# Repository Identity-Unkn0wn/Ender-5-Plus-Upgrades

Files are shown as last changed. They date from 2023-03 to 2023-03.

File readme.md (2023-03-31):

# Ender 5 Plus(E5+) Upgrades

This is just a collection of thing that I have done to my printer and wanted to consolidate the resources for anyone who may want to do the same. 

**WARNING:** This is still a work in progress.

## Table of Contents
- [Installation of Sprite Extruder](#installation-of-sprite-extruder)
- [Installation of BTT SKR 3EZ](#installation-of-btt-skr-3ez)
- [Klipper \& .CFGs](#klipper--cfgs)
- [EXTRAS](#extras)

# Installation of Sprite Extruder
* [Printing Sprite Extruder Parts](Installing%20Sprite%20Extruder/Printing%20Sprite%20Extruder%20Parts.md)
* [Installing Sprite Extruder](Installing%20Sprite%20Extruder/Installing%20Sprite%20Extruder.md)
* [Wiring Extruder](Installing%20Sprite%20Extruder/Wiring%20Extruder.md)

# Installation of BTT SKR 3EZ
* [Printing Motherboard (MB) Adapter](Installing%20BTT%20SKR%203EZ/Printing%20MB%20Adapter%20Plate.md)
* [Installation & Wiring](Installing%20BTT%20SKR%203EZ/Installing%20BTT%20SKR%203EZ.md)

# Klipper & .CFGs
* [Klipper Install](Klipper%20&%20.cfgs/Klipper-Mainsail%20install.md)
* [Flashing Printer MCU](Klipper%20&%20.cfgs/Flashing%20Printer%20MCU.md)
* [Mainsail](Klipper%20&%20.cfgs/Mainsail.md)

# EXTRAS
* [BL Touch (& sim)](Extra/Extra.md)

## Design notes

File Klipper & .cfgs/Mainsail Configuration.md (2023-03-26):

# Configuring Mainsail
This part is strictly how I did mine and you are more than welcome to modify and set up to your liking.

# Printer.cfg
* Select `MACHINE` in menu on the left side
* Find your printer.cfg file and select it
* Below will be what mine looks like, but yours will vary depending on how you set your printer up.
> 
```
# This file contains pin mappings for the Creality Ender 5 Plus.
# Ender 5 Plus stock uses a Creality v2.2 board, similar to CR-20 Pro.
# To use this config, the firmware should be compiled for the AVR
# atmega2560.

# See docs/Config_Reference.md for a description of parameters.

#[include timelapse.cfg] ## uncomment this if you choose to install timelapse feature
#[include macros.cfg] # I use a separate folder for my macros
[include mainsail.cfg]
[virtual_sdcard]
path: /home/ryan/Ender5Plus_data/gcodes ###Change this to your path
on_error_gcode: CANCEL_PRINT

[exclude_object]

######################################################################
# BED LEVELING
######################################################################

[bltouch]
sensor_pin: ^PC13
control_pin: PE5
x_offset:-31
y_offset:-41
#z_offset: 3.380
pin_up_reports_not_triggered: True
pin_up_touch_mode_reports_triggered: False
stow_on_each_sample: False
probe_with_touch_mode: True
speed:10
samples:2

[safe_z_home]
home_xy_position: 175, 175 # Change coordinates to the center of your print bed
speed: 100
z_hop: 10 # Move up 10mm
z_hop_speed: 20

[bed_mesh]
speed: 200
horizontal_move_z: 5
mesh_min: -4, -6
mesh_max: 320, 301
probe_count: 5, 5
mesh_pps: 2,2
fade_start: 1.0
fade_end: 10.0
fade_target: 0.0

[screws_tilt_adjust]
screw1: 58, 74
screw1_name: Front Left screw
screw2: 352, 338
screw2_name: Back Right
screw3: 352,74
screw3_name: Front Right
screw4: 58,338
screw4_name: Back Left
horizontal_move_z: 6
speed: 200
screw_thread: CW-M4

[z_tilt]  ### Will only need this if you connected both z axis motors to their own driver
z_positions: 22, 204
           351, 204
# A list of X,Y coordinates (one per line; subsequent lines
# indented) describing the location of each bed "pivot point". The
# "pivot point" is the point where the bed attaches to the given Z
# stepper. It is described using nozzle coordinates (the XY position
# of the nozzle if it could move directly above the point). The
# first entry corresponds to stepper_z, the second to stepper_z1,
# the third to stepper_z2, etc. This parameter must be provided.
points: 22, 204
      351, 204
          
# A list of X,Y coordinates (one per line; subsequent lines | back |
# indented) that should be probed during a Z_TILT_ADJUST command. | |
# Specify coordinates of the nozzle and be sure the probe is above L z1 z R
# the bed at the given nozzle coordinates. This parameter must be | |
# provided. | front |
speed: 200
horizontal_move_z: 7
retries: 20
# Number of times to retry if the probed points aren't within
# tolerance.
retry_tolerance:0.0025
# If retries are enabled then retry if largest and smallest probed
# points differ more than retry_tolerance. Note the smallest unit of
# change here would be a single step. However if you are probing
# more points than steppers then you will likely have a fixed
# minimum value for the range of probed points which you can learn
# by observing command output.

# This file contains common pin mappings for the BigTreeTech SKR 3.
# To use this config, the firmware should be compiled for the
# STM32H743 with a "128KiB bootloader".

# See docs/Config_Reference.md for a description of parameters.

######################################################################
# X Stepper
######################################################################

[stepper_x]
step_pin: PD4
dir_pin: !PD3
enable_pin: !PD6
microsteps: 16
rotation_distance: 40
endstop_pin: ^PC1
position_endstop: 352
position_max: 352
#position_min:-20  #used for getting my min
homing_speed: 150

[tmc2209 stepper_x]
uart_pin: PD5
run_current: 0.580
diag_pin:
interpolate: False #Comment out if you use stealth shop
#stealthchop_threshold: 999999 #will make your printer quieter, but at a cost to accuracy; this applies to all below

######################################################################
# Y Stepper
######################################################################

[stepper_y]
step_pin: PA15
dir_pin: !PA8
enable_pin: !PD1
microsteps: 16
rotation_distance: 40
endstop_pin: ^PC3
position_endstop: 342
position_max: 342
#position_min:-10
homing_speed: 150

[tmc2209 stepper_y]
uart_pin: PD0
run_current: 0.580
diag_pin:
interpolate: False
#stealthchop_threshold: 999999

######################################################################
# Z & Z1 Stepper
######################################################################

[stepper_z]
step_pin: PE2
dir_pin: !PE3
enable_pin: !PE0
microsteps: 16
rotation_distance: 4
endstop_pin: probe:z_virtual_endstop
#position_endstop: 0.5
position_max: 400
position_min: -6
homing_speed: 10.0

[tmc2209 stepper_z]
uart_pin: PE1
run_current: 0.580
diag_pin:
interpolate: False
#stealthchop_threshold: 999999

[stepper_z1]
step_pin: PD11
dir_pin: !PD10
enable_pin: !PD13
microsteps: 16
rotation_distance: 4
#endstop_pin: PC13
#position_endstop: 0.5
#position_max: 200

[tmc2209 stepper_z1]
uart_pin: PD12
run_current: 0.580
diag_pin:
interpolate: False
#stealthchop_threshold: 999999

######################################################################
# Extruder
######################################################################

[extruder]
step_pin: PD15
dir_pin: PD14
enable_pin: !PC7
microsteps: 16
gear_ratio: 42:12
rotation_distance: 26.4462726999097
nozzle_diameter: 0.400
filament_diameter: 1.750
heater_pin: PB3
sensor_type: EPCOS 100K B57560G104F
sensor_pin: PA2
#control: pid
#pid_Kp: 22.2
#pid_Ki: 1.08
#pid_Kd: 114
min_temp: 0
max_temp: 300
max_extrude_only_distance: 450
min_extrude_temp: 180
#pressure_advance: .1127

[tmc2209 extruder]
uart_pin: PC6
run_current: 0.650
diag_pin:
#stealthchop_threshold: 999999

######################################################################
# Heated Bed
######################################################################

[heater_bed]
heater_pin: PD7
sensor_type: EPCOS 100K B57560G104F
sensor_pin: PA1
#control: watermark
min_temp: 0
max_temp: 130

[fan]
pin: PB7

[heater_fan hotend_fan]
pin: PB6
heater: extruder
heater_temp:50.0

[heater_fan mcu_fan]
pin: PB5
heater_temp: 45.0

[mcu]
serial: /dev/serial/by-id/usb-Klipper_stm32h743xx_400029000B51303138393138-if00

[printer]
kinematics: cartesian
max_velocity: 300
max_accel: 3000
max_z_velocity: 5
max_z_accel: 100

########################################
# EXP1 / EXP2 (display) pins
########################################

[board_pins]
aliases:
    # EXP1 header
    EXP1_1=PC5, EXP1_3=PB1, EXP1_5=PE9,  EXP1_7=PE11, EXP1_9=<GND>,
    EXP1_2=PB0, EXP1_4=PE8, EXP1_6=PE10, EXP1_8=PE12, EXP1_10=<5V>,
    # EXP2 header
    EXP2_1=PA6, EXP2_3=PE7, EXP2_5=PB2, EXP2_7=PC4,   EXP2_9=<GND>,
    EXP2_2=PA5, EXP2_4=PA4, EXP2_6=PA7, EXP2_8=<RST>, EXP2_10=<NC>

[temperature_sensor raspberry_pi]
sensor_type: temperature_host
min_temp: 10
max_temp: 100

[temperature_sensor mcu_temp]
sensor_type: temperature_mcu
min_temp: 0
max_temp: 100

[filament_switch_sensor filament_sensor]
pause_on_runout: True
#runout_gcode: PAUSE
#insert_gcode: RESUME
switch_pin: PC2
```

## Cusomization

From here everything else would be your prefrence. I'll soon add a guide on how I tune my printer. I'll add links for anything I think would be useful in the [Extra](../Extra/Extra.md) section.

<sub>[Extra](../Extra/Extra.md)

<sub>[Main](../readme.md)

<sub> [Top](#configuring-mainsail)

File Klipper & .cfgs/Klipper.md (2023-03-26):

# Installing Klipper
What a trip we've had right, sit tight were almost done.

## Prep an OS image
* Download OS
  * Insert Micro SD card into computer
  * Download *[Raspberry Pi Imager](https://downloads.raspberrypi.org/imager/imager_latest.exe)*
  * Once installed select `Choose OS`
   > * **NOTE:** If it gives an error about downloading an OS directory, exit and open it back up, seems to be a common issue(maybe for just me?).
  * Scroll to `Raspberry Pi OS (Other)` and select
  * Scroll to `Raspberry PI on Lite (64 bit)` and select
    > * You will see a settings icon appear, we will get to that shortly
  * select `Choose Storage`
    > * Please please please make sure you select the correct storage device Don't come crying on here that I caused your hard drive to be wiped. I have yet to see any of mine show up but I have see YT vids of it happening.
  * Select the `Settings Icon` on the bottom right
  * *Optional:* You can set your host name, just be sure you remember/ write it down it will come into play later.
  * Scroll to `Enable SSH` and enable the box
  * Scroll down from there and set your SSH `User Name` & `Password`
  > * WRITE THIS DOWN; YOU WILL NEED IT LATER!
  * *Optional:* Configure your wireless LAN 
  >  *  This part is optional if your intent is to use a wired connection, nothing is needed here.
  > * Don't forget to set your `Wireless LAN Country` (example: if you're in good ole 'Murica scroll to select `US`)
  * Next, select `Set Local Settings` 
  >  * Set things to your local setting
  * Select `Save`
   > * Window will close
  *  Select `Write`
 > My computer usually pops a notification, just ignore or close them out. This part may take a while, just sit tight and let it finish. Once it's complete it will auto eject the drive.

## Installing Raspberry Pi OS
Buckle up this one is going to be a long one.
* if your Pi is powered up, turn it off
* Insert SD card into SD card slot on said Pi
* Power the Pi up    
* Wait a few minutes
* Then it should be done
* :P
  
## SSHing into your Raspbeery Pi
Ok so there are other ways of doing it, like Putty, but I like using Windows powershell. Most of the steps should be the same either way. If this is your first time using a terminal I promise its not that scary. Well here we go!
* SSH into your Raspberry Pi from a terminal:
  * Open up your favorite terminal
  * Type in `ssh username@your IP address`
   > * You can find your IP address from your router or a program like  [Advanced IP Scanner](https://www.advanced-ip-scanner.com/download/)
   > * You set up your user name in the "[Prep an OS Image](#prep-an-os-image)" section.
   > * If you ste up a hostname it will be *"username@whateveryouput.local"*
     * It will then give you a *"warning"* about its authenticity, and if you want to continue type `yes` and press enter
  * Enter your `password` when prompted. 
  > * *Note: The password you type will not appear, but it is there.*
  * Enter `sudo apt-get update`
  * Enter `sudo apt-get upgrade`
  > * If it ask you to continue, just press enter; yes is the default. This sometimes take a minute or two, be patient.
  * Enter `sudo reboot`
  * Give it a minute or two then SSH back into your Raspberry Pi.

## Installing Klipper/ User Interface (UI)
For this portion I'll be using Mainsail as my UI You don't have to use this program, but I've tried Fluidd and Octoprint and while on Marlin I did like Octoprint, Mainsail just jives better for me with Klipper. 

This method is not for everyone, but I can definitely say beginners will probably like this route better than figuring out through the klipper website. Additionally, on the KIAUH website it says the `Raspberry Pi OS Lite (32bit)` is compatible, but I've been using the 64 bit version for a few months and its been working without issue.

* Install git `sudo apt-get install git -y`
* Use this command to download KIAUH into your home directory `cd ~ && git clone https://github.com/th33xitus/kiauh.git`
* Next, you will start KIAUH with `./kiauh/kiauh.sh`
> * Don't be afraid of the interface that pops up after pressing enter
* Type in `1` and press enter
> * This will take you to the install menu
* Type in `1` again and press enter
> * This will start the process of installing Klipper
* Next type `1` to install recommended version of Python and press enter
* Next type in the number of instances of klipper you would like to install
> * You will need 1 per printer
> * if you type in more than 1 instance it will confirm the amount, just hit `Enter` yes is the default
* Next it will give you the option of creating custom names, you can do this later so just enter No is the default.
> * It will now begin installing however many instance of klipper you chose, be patient and let it do the work.
* One that is finished, it will ask to add user to group, hit enter as Yes is the default. 
> * If you hit no you will not have the permissions you need to get to the printer
 * From here it will take you back to the instillation UI screen
 * Now we will install moonraker, Type `2` and press enter
 * it should detect how many instances of klipper you installed and display it, if not type that number in and press enter.
 > * *NOTE:* If you have more than one instance, it will ask you to confirm the amount you want to install. Hit enter as Yes is the default.
 * This should be quick, but if not, be patient and let it install.
 * Once this is complete It will take you back to the instillation UI again.
 > * *NOTE:* If you have more than one, all of your instances will appear with their IP address.

> Example:

<div align="center">

|Instance Number|IP Address |
|:---:|:---:|
| Instance 1: |192.168.696.969:7125|
| Instance 2: |192.168.696.969:7126|
</div>

> From here the instance number will continue to rise for the amount of instances you installed and only the digits after the ":" will rise by one number.
* Okay, moving on. Next up, you will want to type `3` to begin installing Mainsail.
> * *NOTE:* It will immediately begin installing
> * *NOTE:* You don't have to choose Mainsail, but that is what I will be continuing on with.
> * *NOTE:* You only need one instance of Mainsail to control all of your printers
* It will pause mid install and ask if you want to install recommended macros, press enter.
* Wait for it to complete and will boot you back to the install UI
* Install complete!
* Type ` b` and press enter to go back to the main menu
* Type ` q ` and press enter to quit out of KIAUH

> * *Note:* Feel free to install crowsnest before exiting out, but I will not be covering that(unless enough request are submitted).

<sub> [Flashing Printer MCU](Flashing%20Printer%20MCU.md)

<sub> [Home](../readme.md)

<sub> [Top](#installing-klipper)

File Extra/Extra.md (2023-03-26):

# Extra
This will be just a curation of vids and whatnots of things i've found useful in setting up and running my printers. Use at your own risk, if I get enough intrest I'll add a step by step guide for them.

## BL Touch(and similar) Setup
* Not going to put much here, the dude in the link below does a great job of explaining the how to. Like the vid for him!
> * https://youtu.be/5vmjBXvY6BA

<sub> [Home](../readme.md)

<sub> [Top](#extra)

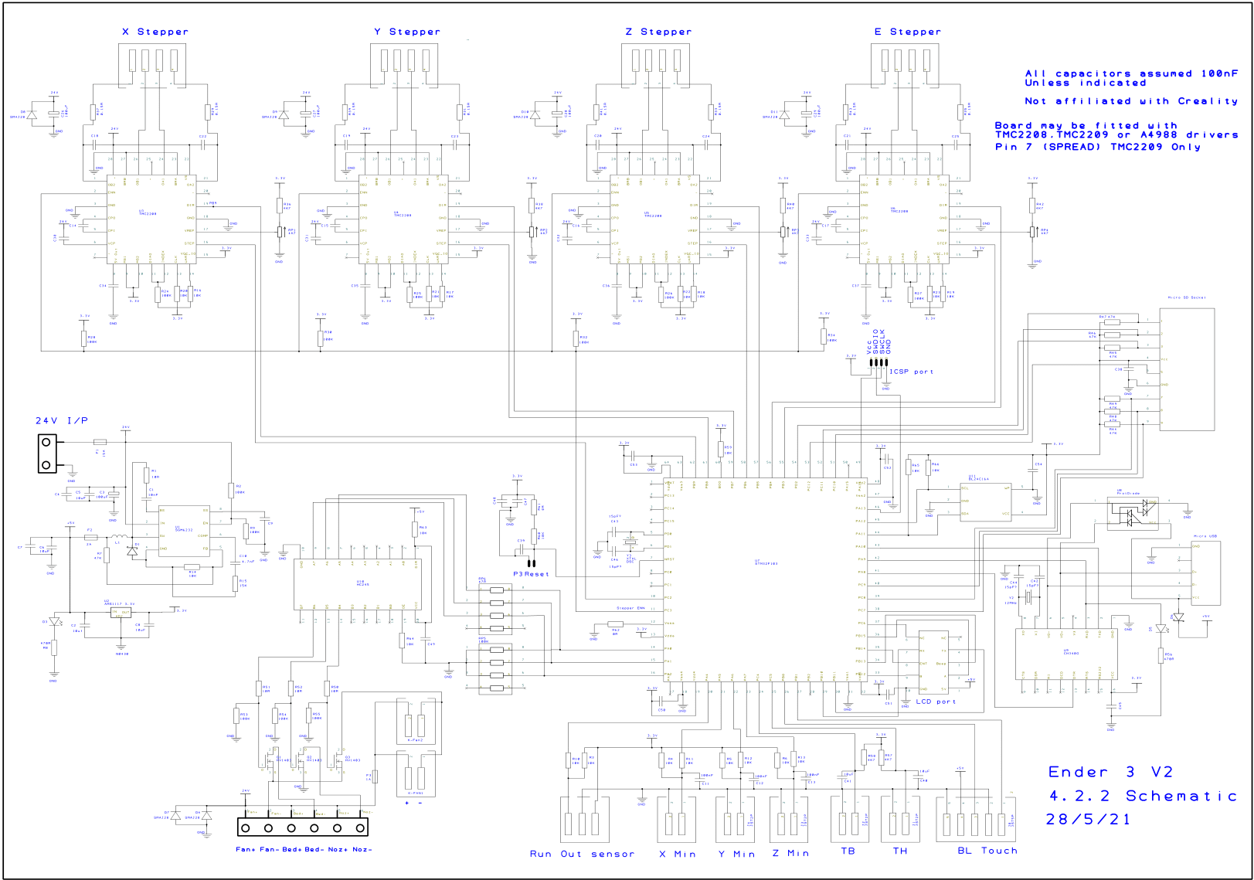
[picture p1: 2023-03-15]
Files/Creality 4.2.2 Schematic-1.png

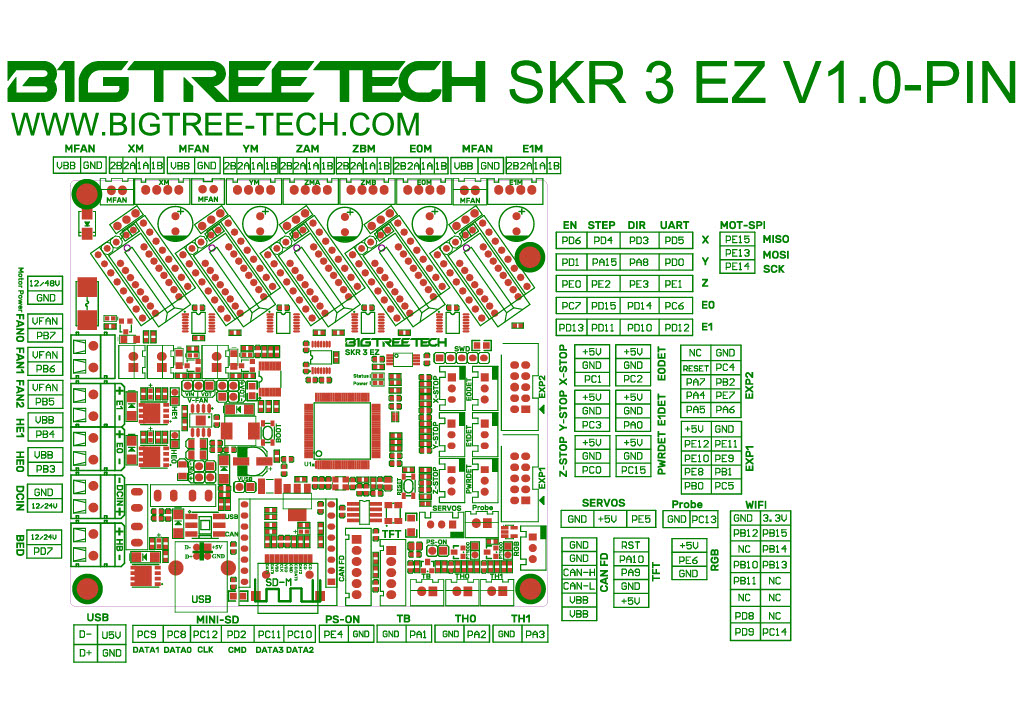
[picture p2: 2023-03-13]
Files/BIGTREETECH SKR 3 EZ Pinout.jpg

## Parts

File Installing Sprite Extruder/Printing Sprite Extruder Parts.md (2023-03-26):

# Printing Sprite Extruder Parts
I have created two variations of the mounting system. The first one is more of an adapter plate and second a mounting system. The point of both of these were to not have to cut belts or do anything to janky. BLUF if you can only print PLA & PETG [Adapter Plate](#adapter-plate) is what you want to go with. In my testing both my PLA and PETG [Mount](#mount) melted where the bottom wheel bolt head is, so use at your own risk!

## Adapter Plate

* Get [Adapter Plate](../Files/E5+%20Adapter%20Plate.stl)
* Print it
    * Print Settings:
        * Nozzle size 0.4 mm
        * Layer and inital Layer height: 0.2 mm
        * Line width: 0.48 mm
        * Wall line count: 5 (you can do less, just add infill)
        * Top/Bottom: 2 (done this way intentionnal)        
        * Print thin walls : ☑️
        * infill: 0% (won't need any with 5 walls)
        
    > **Note:** Everything is really your prefrance, this is just what has worked for me. Outside of what I provided will be up to what you have your printer tuned for and nozzle diameter.

## Mount

* Get [Mount](../Files/Ender5+%20Mount.stl)
* Print it
    * Print Settings:
        * Nozzle size 0.4 mm
        * Layer and inital Layer height: 0.2 mm
        * Line width: 0.48 mm
        * Wall line count: 5 (you can do more and have 0 infill)
        * Top/Bottom: 2 (done this way intentionally)
        * Alternate Extra wall: ☑️
        * Print thin walls : ☑️
        * infill: 50% (your descretion)
        * Infill Pattern: Gyroid (your descretion)
        * Supports: off (this depends on how much you trust your print settings/ tuning)
        
    > **Note:** Everything is really your prefrance, this is just what has worked for me. Outside of what I provided will be up to what you have your printer tuned for and nozzle diameter. **REMINDER:** This [Mount](#mount)  will melt if the filament used doesn't have a high temp threshold.

# Extruder Cable Mount
This next item is optional, if you have a better method you want to use go ahead, but the cable harness will drag on the Y-axis stepper motor and bars.

* Get [Cable Mount](../Files/Extruder%20Cable%20Mount.stl)
    * Print Setting:
         * Nozzle size 0.4 mm
        * Layer and inital Layer height: 0.2 mm
        * Line width: 0.48 mm
        * Wall line count: 4 (my default)
        * Top/Bottom: 4 (my default)
        * Alternate Extra wall: ☑️
        * infill: 50% (your descretion)
        * Infill Pattern: Gyroid (your descretion)
        * Supports: off (this again depends on how much you trust your print settings)
    > **Note:** Everything is really your prefrance, this is just what has worked for me. Outside of what I provided will be up to what you have your printer tuned for and nozzle diameter.
        
    * Items you will need
        * Top cover needs needs:
            * x4 - M4x8 Screw [(Kit I use)](https://amzn.to/3FqGRln)
            * x4 - M4 Nut [(Kit I use)](https://amzn.to/3FqGRln)
        * Base will need:
            * x2 - M3x8 screw [(Kit I use)](https://amzn.to/3FqGRln)
            * x2 - M3 T-nut [(Kit I use)](https://amzn.to/3yGxaM2)

<sub>[Installing Sprite Extruder](Installing%20Sprite%20Extruder.md)

<sub>[Main](../readme.md)

<sub>[Top](#printing-sprite-extruder-parts)</sub>

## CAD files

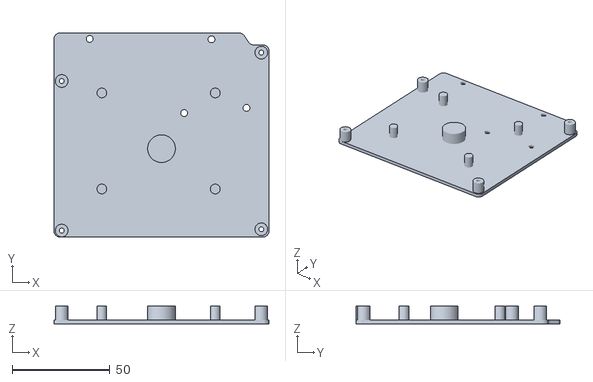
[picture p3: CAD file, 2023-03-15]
Files/SKR mount.stl
109.7 x 104.1 x 9.00

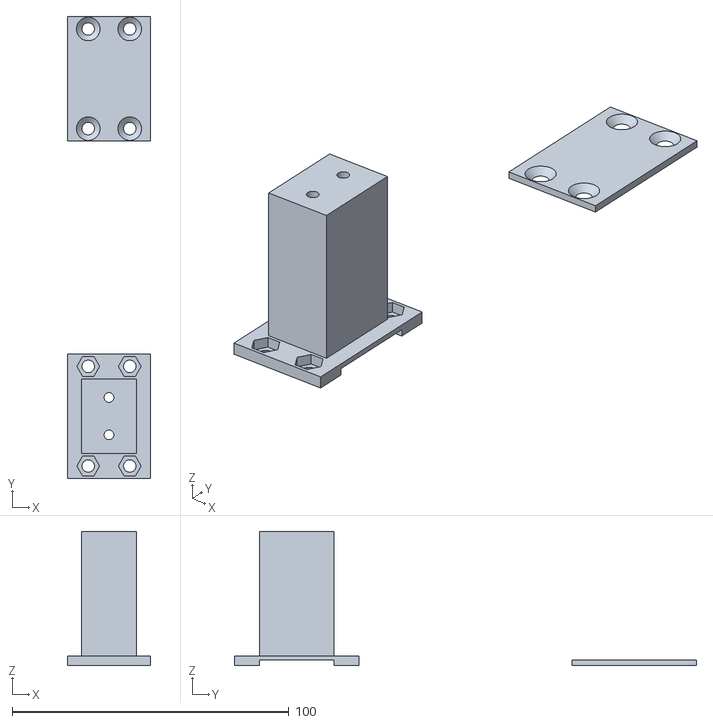
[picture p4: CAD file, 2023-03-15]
Files/Extruder Cable Mount.stl
30.0 x 166.9 x 48.5

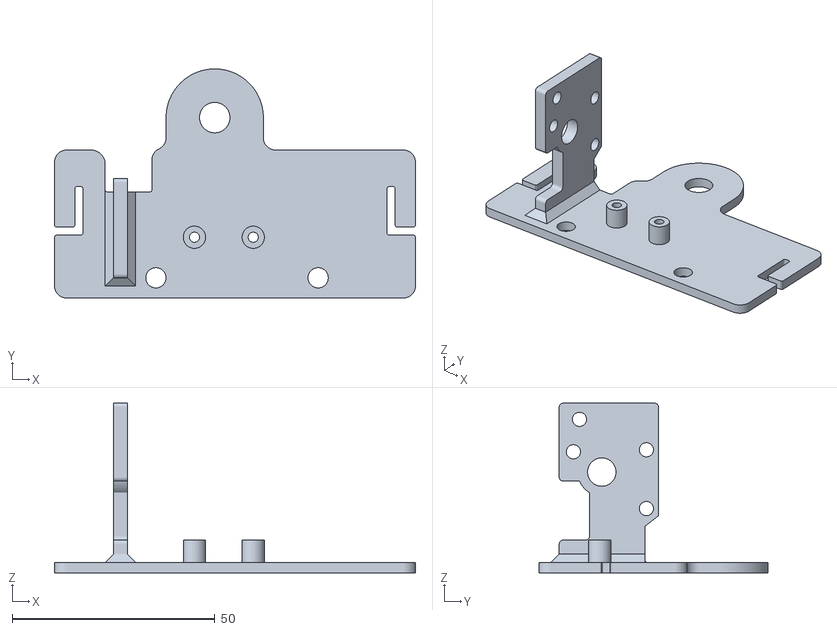
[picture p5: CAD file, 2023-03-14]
Files/Ender5+ Mount.stl
89.0 x 56.5 x 41.9

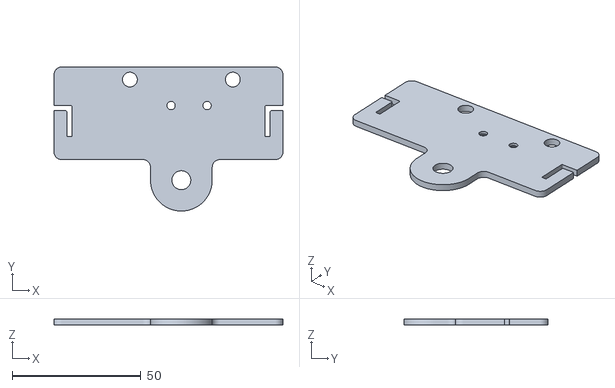
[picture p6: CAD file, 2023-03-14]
Files/E5+ Adapter Plate.stl
89.0 x 56.0 x 2.50

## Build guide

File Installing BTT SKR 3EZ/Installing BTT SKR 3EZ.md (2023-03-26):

# Installing BTT SKR 3EZ
This is fairly simple process. Additionally, I'm not going to type step by step on wiring, there will be a link to that. If you wired one, its basically the same.

## Step 1: Poweing off
* Turn the power off and disconnect the power cable.

## Step 2: Open the electronics compartment
If you are a visual learner go [here](https://youtu.be/l7mxGVF-QGE?t=86) down below will just be typed stepps.
> **NOTE:** *You can ignore most of this if you plan on flipping your printer.*
* Unplug/ remove SD card
* Optional but reccommended; remove right side stepper motor wire (makes it easier to flip over the electronics enclosure) if you just want to flip your enclosure and not the printer
* Remove the 4 black screws; two in the front and two in the back of the printer.
* Flip over case
* Remove 6 screws holding the bottom to the top.

## Step 3: Remove Stock board
Make sure you take out the MB and not the screen, not being a SA just through as I can be. My visual learners go [here](https://youtu.be/l7mxGVF-QGE?t=171).

* There a 4 screws on the board that needs to be removed (save those screws they will be reused)
* Remove the cables
* Set the board aside (and take a moment of silence for its hard work)

## Step 4: Installing the MB
Almost done! 

* Grab your handy dandy board adapter and you stock MB screws
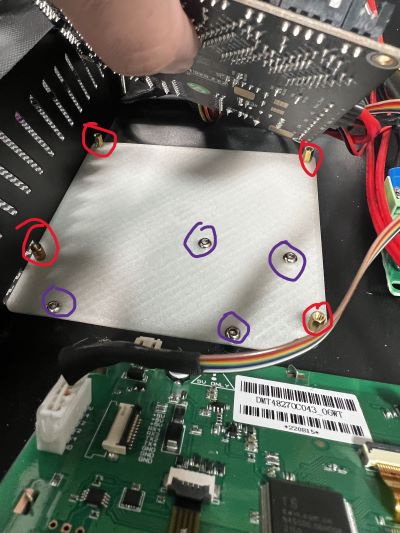
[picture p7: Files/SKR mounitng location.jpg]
MB Adapter
    > 
    > * Purple: This is where your stock screws holding your MB will go.
    > * Red: this is where your M2.5*6+6 [kit I used](https://amzn.to/3JkD8qF)
* Next up install your MB with M2.5*6 screws 
> **Note:** *MB orientation is with USB facing power supply*

## Installing your cables
This will mostly be the same for everyone. Instead of typing it all out click [here.](https://youtu.be/r9fsRMXb5X0?t=550) He does a really good job of explaining it and why recreate the wheel?
> **NOTE:** *One thing to point out I highly recommend if you're following along with this from my sprite extruder installation double check the ohms on both fan pins to make sure their polarity is correct before plugging it in. Remember don't take the readout as anything except if it's wired correctly you will get some numbers if not then zero.*

> **NOTE:** *If you want the ability to run Z tilz add your second Z cable to the 5th stepper driver port.(E1M)*

* ## **NOTE:** *My extruder didn't work with the way it came. Yours probably won't either since the creality boards extruder pinout show their wire sequence different. Explination below.*

**EOM Pin Sequence on SKR**
|Set 1 | |Set 2| |
|:----:|:--:|:---:|:--:|
| 2B | 2A |  1B | 1A |

> See pinout [here.](../Files/BIGTREETECH%20SKR%203%20EZ%20Pinout.jpg)

**E1 Pin Sequence on Stock 4.2.2 Ender 3 Pro MB**
|Set 1 | |Set 2| |
|:----:|:--:|:---:|:--:|
| 2B | 1B |  1A | 2A |
> * What they were made to go on.
> * See schematic [here.](../Files/Creality%204.2.2%20Schematic-1.png)

* So all that to say do a continuity test and the two that cause your multimeter to beep put them side by side. If you want to be certan test both sets once you swap the two. Doesn't matter which one is **"A"** or **"B"** in the set as long as they are cozy side by side.

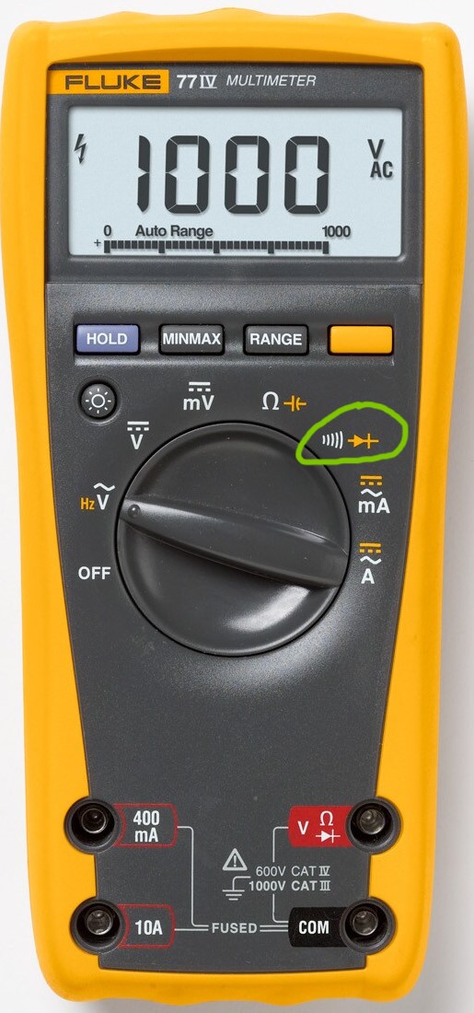
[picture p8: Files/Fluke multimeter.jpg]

> Green: most multimeters continuity test logo should look like this.

* Lastly for instillation is your USB Cable. 
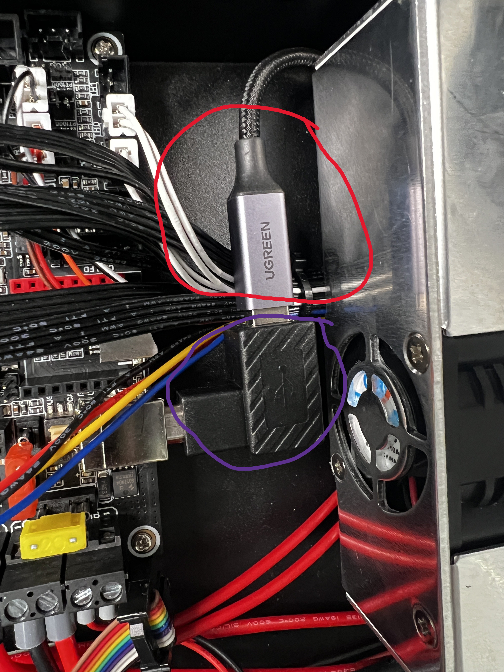
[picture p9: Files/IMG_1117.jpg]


    > **Purple:** I purchased this [left angle adapter](https://amzn.to/3FrYykr).
    
    > **RED:** As well as a much [longer cable](https://amzn.to/3YOFiVd) to be ran out the back

> # Don't close up shop just yet. Need to flash the board before closing up. If you know how to set up klipper then you are good to go from here.

<sub>[Klipper-Mainsail Configuration](../Klipper%20&%20.cfgs/Klipper.md)

<sub>[Home](../readme.md)

<sub>[Top](#installing-btt-skr-3ez)

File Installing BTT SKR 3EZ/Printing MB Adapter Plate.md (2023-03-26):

# Printing the Motherboard Adapter Plate
As with everything on here this is what worked for me and I designed the board for exactly what I wanted. You can choose a different mounting method if you choose. I wont be mad at you. 
> * **NOTE:** *You will need a M2.5 standoff and screws for this mount. [Kit I used.](https://amzn.to/3JkD8qF)*

## MB Adapter Plate

* Get [SKR Mount](../Files/SKR%20mount.stl)
* Print it
    * Print Settings:
        * Nozzle size 0.4 mm
        * Layer and inital Layer height: 0.2 mm
        * Line width: 0.48 mm
        * Wall line count: 4 (my default)
        * Top/Bottom: 4 (my default)        
        * infill: 15% (your descretion)
        * infill pattern: gyroid (your descretion)
        
> **NOTE:** *Everything is really your prefrance, this is just what worked for me. Outside of what I provided will be up to what you have your printer tuned for and nozzle diameter.*

<sub>[Installing BTT SKR 3EZ](Installing%20BTT%20SKR%203EZ.md)

<sub>[Home](../readme.md)

<sub>[Top](#printing-the-motherboard-adapter-plate)

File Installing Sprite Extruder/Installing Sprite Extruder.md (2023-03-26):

# Installing Sprite Extruder
This is mostly self explanitory, but for the sake of flow I will add this section. For steps 1 and 2 I will not be going into to much detail as you can just reverse the steps you took while assembling your printer. [Manual](https://www.creality.com/pages/download-ender-5-plus) 

> **NOTE:** *MY SPRITE PRO KIT DID NOT COME WITH A CABLE FOR THE BL TOUCH. CHECK YOURS! [The one I purchased.](https://amzn.to/3ZOp1AR)*

> **NOTE:** *I will not be taking pictures or an install guide on the mount itself, but if you're going that route its the same general steps.*

> **NOTE:**  *If you have not printed all of the parts please click [here](Printing%20Sprite%20Extruder%20Parts.md).*

## Step 1: Power
* Verify printer's power is off; unplug if you feel like it

## Step 2: Remove stock hotend
* Remove original hotend. Save all wheel hardware and screws holding hotend to mounting plate. Follow this [video](https://www.youtube.com/watch?v=nbmqpncobn8) if you do not know how to do this.
* Loosen belt tensioner on the left side of the X-axis.
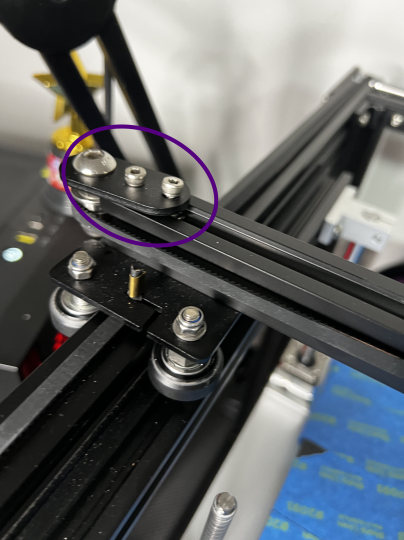
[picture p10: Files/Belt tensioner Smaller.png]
Belt Tensioner
> 

## Step 3 Attach Adapter Plate
* Begin by attaching the Adapter Plate to the mount that comes with the sprite extruder.
>Step 3
 > * Purple - reuse screws holding the factory extruder onto original plate. The chamferd holes will be facing away from the extruder plate to make the screws more flush.
 > * Red - This will all be pulled off original 

## Step 4 Attach Sprite Extruder to X-Axis
* Attach Extruder mount to X-Axis

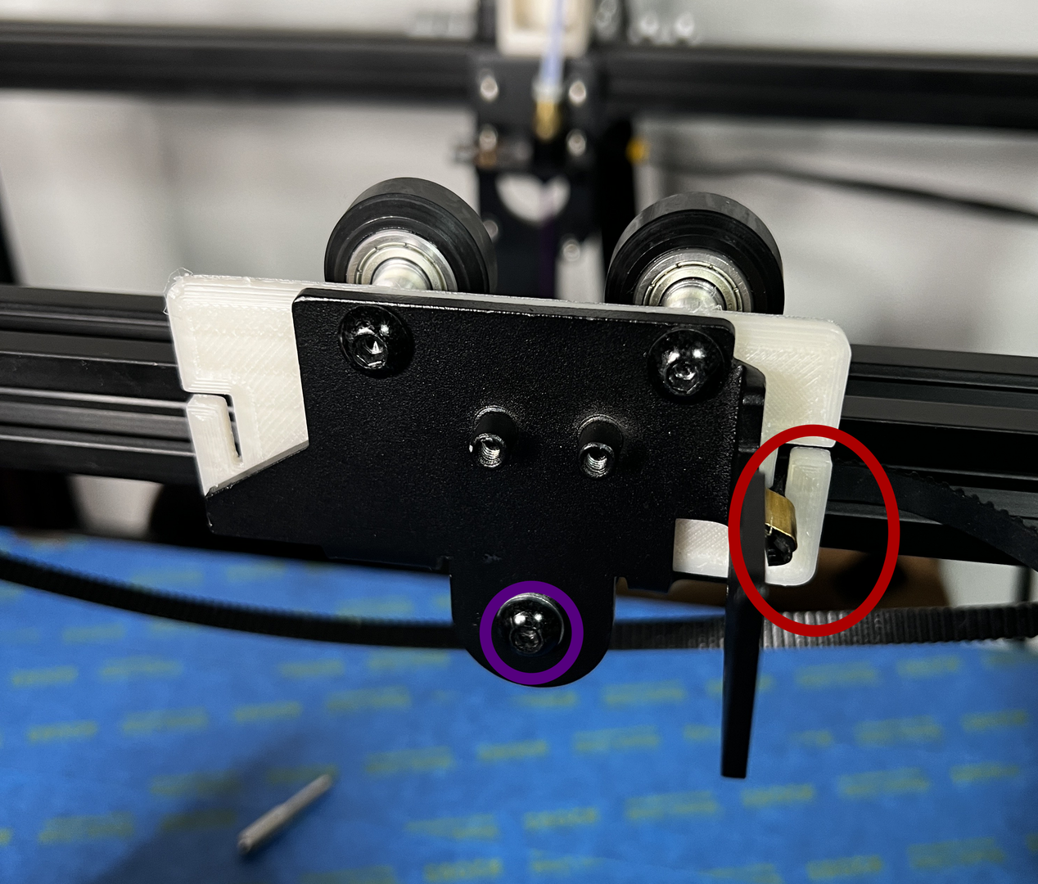
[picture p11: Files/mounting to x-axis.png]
>
 > * Red - I like to connect one side fo the belts before attaching the mount to the rail, you can do both after just, wanted to point this out.
 > * Purple - place both top wheels in the V-slot and insert lower stock bolt and other hardware.
 > * At this time you should adjust the eccentric nut. Ensure the carrage can freely move side to side, but doesn't wiggle(?). 
 > * lastly in this step attach the other side of the belt (or both sides if you waited.)

 ## Step 5
  * Attach Sprite Extruder (ignore my cable my pictures are form after install and testing)
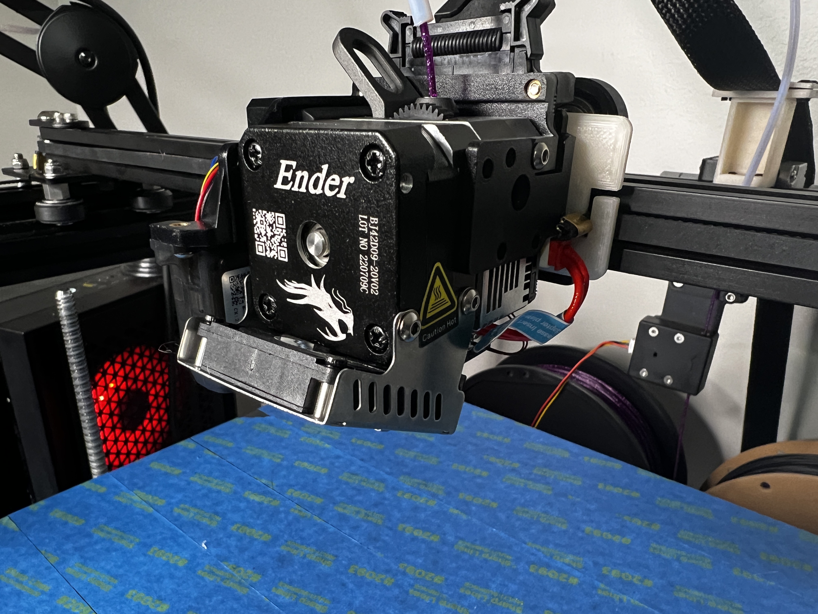
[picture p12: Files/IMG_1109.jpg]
> 
    > * You will know it has attached correctly if it stays put once you (carefully) let it go. You can also wiggle it a little and you'll feel it's slightly "locked" inplace.

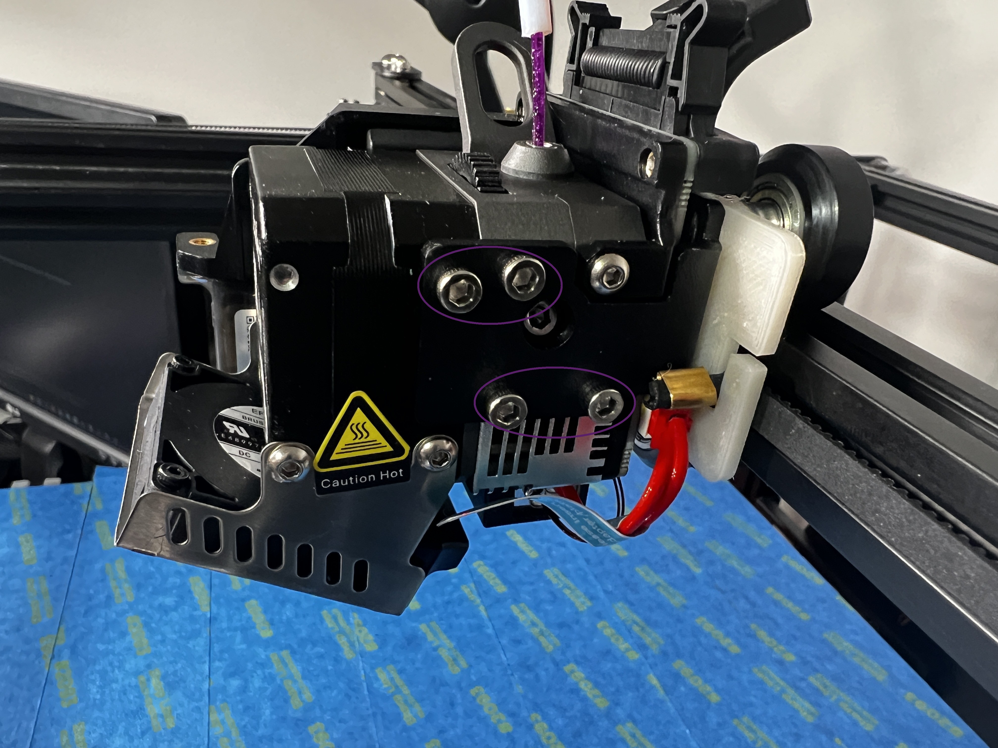
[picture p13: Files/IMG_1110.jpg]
> 
    >  * Then attach the 4 bolts that came with the kit. 

<sub>[Wiring Extruder](Wiring%20Extruder.md)

<sub>[Main](../readme.md)

<sub>[Top](#installing-sprite-extruder)

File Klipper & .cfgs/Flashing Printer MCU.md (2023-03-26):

# Flashing Printer MCU
So this part isn't really that hard, but you do have to pay attention to what you're selecting. I will place a link with the vanilla .cfg files from Klipper. You are more than welcome to use mine and change it, but remember this is what works for me and you will want to adjust for your preferences.
> * *Reference:* [Klipper Config SKR 3](https://github.com/Klipper3d/klipper/blob/master/config/generic-bigtreetech-skr-3.cfg) / [Ender 5 Plus](https://github.com/Klipper3d/klipper/blob/master/config/printer-creality-ender5plus-2019.cfg) vanilla files

## Building MCU Firmware
This for the BTT SKR 3 EZ
* In your terminal, insert ` cd ~/klipper/ ` and press enter
* insert ` make menuconfig ` and press enter
> * **NOTE:** *A menu will apppear well go through it*
* press the space bar to ` Enable extra low-level configuration options `
* Arrow down to ` Processor model (***) ' (* it'll have something stock here) and press enter
* Arrow down until you see ` STM32H743 ` and press enter
* Ensure ` Bootloader offset ` is set to ` 128kiB `
* Arrow down to ` Clock Refrence ` and press enter
* Arrow down to ` 25 MHz crystal ` and press enter
* Everything else here can stay the same
* Press ` q ` 
* When dialog box appears type ` y `. This will bring you back to the main screen.
* insert `make ` and press enter

## Flashing MCU
You will need the SD card that came with your printer (or similar). to be inserted into your computer at this time.
* Open up WinSCP ([downlad](https://winscp.net/eng/download.php))
* Ensure ` SFTP ` is selected
* Insrt your host name(this will be your IP address)
* Insert your user name and password
* Select ` Login `
> * **NOTE:** *On the left hand side you will want to ensure you open the folder where your removable drive is*
> * **NOTE:** *On the right will be your raspberry pi folders and where this next section will refering to*
* ensure you are in path `/home/(your username)/klipper/out
* drag and drop the ` klipper.bin ` file over to the sd card side
* rename the file to ` firmware.bin `
* close out of the program
* eject the sd card out of the computer
> * **NOTE:** *Ensure your printer is off at this point*
* Insert your sd card into the MCU 
* power on the printer
* I usually let the printer sit for 5ish minutes to ensure its flashed, but it doesn't really take that long.
* Power off and remove SD card
> * **NOTE:** *MCU should be flashed at this point, to verify insert SD card back into PC and check that the file has gone form `firmware.bin` to `FIRMWARE.bin` the all camps firmware is your confirmation*

## Serial Port Path
This part might be better off in another section, but since were not in the UI just yet best to just grab this information now.
> * **NOTE:** *Your printer should be connected to your raspberry pi at this point.*
* Open up your terminal of choice
* insert ` ls /dev/serial/by-id/* `
> * **NOTE:** *It should display something like this `/dev/serial/by-id/usb-Klipper_stm32h743xx_400029000B51303138393138-if00`*
* Copy your serial address to somewhere you can get to later on.

<sub> [Mainsail Configuration](Mainsail.md)

<sub>[Home](../readme.md)

<sub>[Top](#flashing-printer-mcu)

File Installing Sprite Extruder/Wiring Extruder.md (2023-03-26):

# Wiring Sprite Extruder
Firstly, this isn't the only way to do it, just the way I chose to do it. Why? well I didn't want to bend any of the vent ports or drill any holes. 

## Step 1: 
* Crimp Cables to match stock cables
* **You will not need to touch original X, Y, Z-Axis, filimant run out, heated bed themistor, or heated bed power cable.**
* I Just took the cables out one by one, crimped them and placed them in the new one as I got done so I didn't have 5 wires loose and not know what order to put them in.

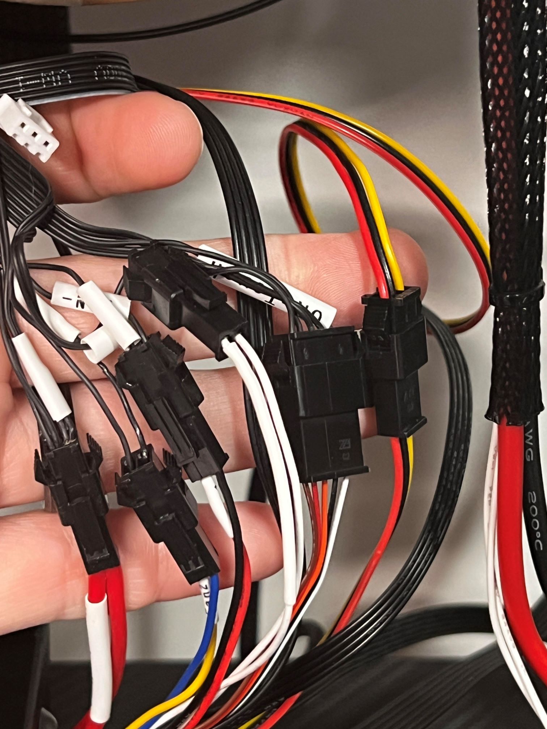
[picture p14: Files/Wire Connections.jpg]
Wiring
> 
> * Video on how to crimp connections [here](https://www.youtube.com/watch?v=GZOh1NzqzzU).
> * [This is the kit I used.](https://amzn.to/42i6e2O)

* One thing I would like to point out is to verify the ohms on the fans, mine was wired weired and the parts cooling fan caused my [BTT SKR E3 Mini V3](https://amzn.to/3ZG8Rtn) board I was testing with to burn out. you will know which is posititve when you connect the red to the positive and the black to the negative it will give you a reading, if it is reversed then it will read "0". Keep in mind the numbers won't tell you anything meaningful, just an easy way to tell polarity.
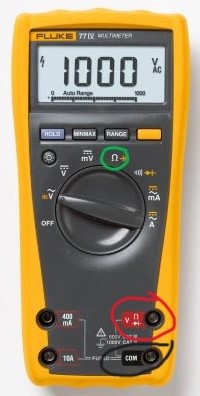
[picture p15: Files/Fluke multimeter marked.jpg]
> 
    > * Green: Mode to test on
    > * Red: Positive Lead
    > * Black: "Negative" lead
    > * [The multimeter I used.](https://amzn.to/3FrEbUu)

## Step 2: Connect Cables
Really not much to say here other than now that you have crimped all the cables with the new connections they should all go into place. 
> **Note:** Remember to note which fan you plug into with fan plug. They are labled Fan and k-fan on the extruder side. I have k-fan connected to the yellow and blue(parts) fan pair and this was the correct.

<sub>[Printing MB Adapter Plate](../Installing%20BTT%20SKR%203EZ/Printing%20MB%20Adapter%20Plate.md)

<sub>[Home](../readme.md)

<sub>[Top](#wiring-sprite-extruder)

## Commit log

2023-03-13 inital add
    [macros.cfg, printer.cfg, timelapse.cfg]
2023-03-14 added more info
    [E5+ Adapter Plate.stl, Ender5+ Mount.stl]
2023-03-14 fixed links
    [Extruder Cable Base stl attempt.stl, Extruder Cable Base.stl, Extruder Cable Mount.3mf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]
2023-03-15 more updates
    [Extruder Cable Mount.3mf, Extruder Cable Mount.stl]
2023-03-15 Update Installing Sprite Extruder.md
2023-03-15 Update Printing Sprite Extruder Parts.md
2023-03-15 More changes
    change the flow; delete cfg file
    [macros.cfg, printer.cfg, timelapse.cfg]
2023-03-16 Started klipper install
    started adding infor klipper install still need vid links
